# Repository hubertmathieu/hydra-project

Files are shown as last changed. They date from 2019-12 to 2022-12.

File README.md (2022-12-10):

# Hydra-Project

Répositoire du projet de serre hydroponique connectée du Cégep de Sorel-Tracy. 

## Introduction

Le projet repose sur une serre flottante qui puise l’eau nécessaire à même la rivière sur
laquelle elle repose. L’eau est filtrée et fertilisée par des engrais naturels solubles dans l’eau.
Elle est ensuite acheminée aux racines des plantes par un évaporateur. C’est une version
plus évoluée de l’hydroponie appelée aéroponie. Les plantes se nourrissent des nutriments
et relâchent dans la rivière une eau purifiée après condensation.

### Prérequis 

Vous trouverez ci-dessous la liste des matériaux ainsi que la liste des différents logiciels qui permettront de faire fonctionner le système d'automatisation de la serre. 
  
| Électronique | Tuyaux et plomberie | Serre et autres | 
| ---| --- | ---|
| [2x Relais 5V](https://amzn.to/2rm3FQe)| [Pompe à eau grand débit](https://amzn.to/2pLP6oq) | [Serre](https://amzn.to/33eJiS8) | 
| [6x Capteur d'humidité](https://amzn.to/2OKojkT) | [Pompe à eau petit débit](https://amzn.to/37F01RS) | [Scellant](https://bit.ly/37GrR0q) |
| [3x Capteur de pH](https://amzn.to/33jcuY7) | [Répartiteur de tuyaux](https://amzn.to/35Dt0nz) | [Disque rotatif](https://amzn.to/34mzRkX)| 
| [5x Capteur de niveau d'eau](https://amzn.to/2XVFi8h) | [3x Buse 50 microns](https://bit.ly/2DeN8js) | [Bac de rangement](https://bit.ly/34lHJTV) | 
| [1x FIPY](https://bit.ly/2KRR1iP) | [Ponceau 12po diamètre x 8po long](https://bit.ly/2OKOisl) | [pH Down](https://amzn.to/33lkYy6) | 
| [1x Filtreur](https://amzn.to/2XLTqAy) | [Rouleau de tuyeau en vinyle](https://bit.ly/33ljoMG) | [Engrais](https://amzn.to/2qJ6oTC) | 
| [2x Module Bluetooth](https://amzn.to/34l5aN6)| [Ruban d'étanchéité](https://amzn.to/2qKvdia) | |
| [9x Valves solénoïdes](https://amzn.to/2DeVWWT) | [50x Colliers de serrage en plastique](https://bit.ly/2KPPf1u) |
| [Convertisseur 12V-5V](https://amzn.to/2KV8RkR) | [Tuyeaux de cuivre (30' x 1/2")](https://bit.ly/2Djcwoq) | |
| [Convertisseur 12V-3.3V](https://amzn.to/2QRFST0) | | | 
| [Convertisseur 120V-12V](https://amzn.to/2QPPcqd) | | |
| [2x Arduino Uno Rev2](https://bit.ly/2pRjQEL) | | |
| [Panneau de distribution](https://amzn.to/2QPEYGv) | | | 
    
### Installation

La prochaine étape consiste à mettre sur pied un serveur Node Express. Nous avons utilisé la distribution Debian dans cet exemple. 

Installez nodeJS, Git et MongoDB, puis vérifiez la version de l'installation. 
```
$sudo apt-get update
$sudo apt-get install nodejs
$node -v
$sudo apt-get install git-all
```

Clonez le répositoire du projet. 
```
$git clone https://github.com/LudoB99/hydra-project.git
$cd hydra-project/backend
$npm install
$cd vendor
$npm install
```

Démarrez le serveur 
```
$cd hydra-project/backend
$docker compose up
```

## Écrit avec l'aide de:

* [NodeJS](https://nodejs.org/en/docs/) - Runtime JavaScript 
* [Express](https://expressjs.com/fr/) - Infrastructure Web
* [MongoDB](https://www.mongodb.com/fr) - Base de données

## Auteurs

* **[Cégep de Sorel-Tracy](https://cegepst.qc.ca)**
* Voyez aussi la liste des [contributeurs](https://github.com/LudoB99/hydra-project/graphs/contributors) qui ont participé au projet.

## License

This project is licensed under the MIT License - see the [LICENSE.md](LICENSE.md) file for details

## Remerciements

* À Alexandre Vovan pour ses conseils judicieux.
* Au [Camping-Marina Parc Bellerive](https://www.campingmarinabellerive.com/) pour leur hospitalité. 
* À la [SADC Pierre-de Saurel](https://sadcpierredesaurel.ca/) pour leur infinie générosité.

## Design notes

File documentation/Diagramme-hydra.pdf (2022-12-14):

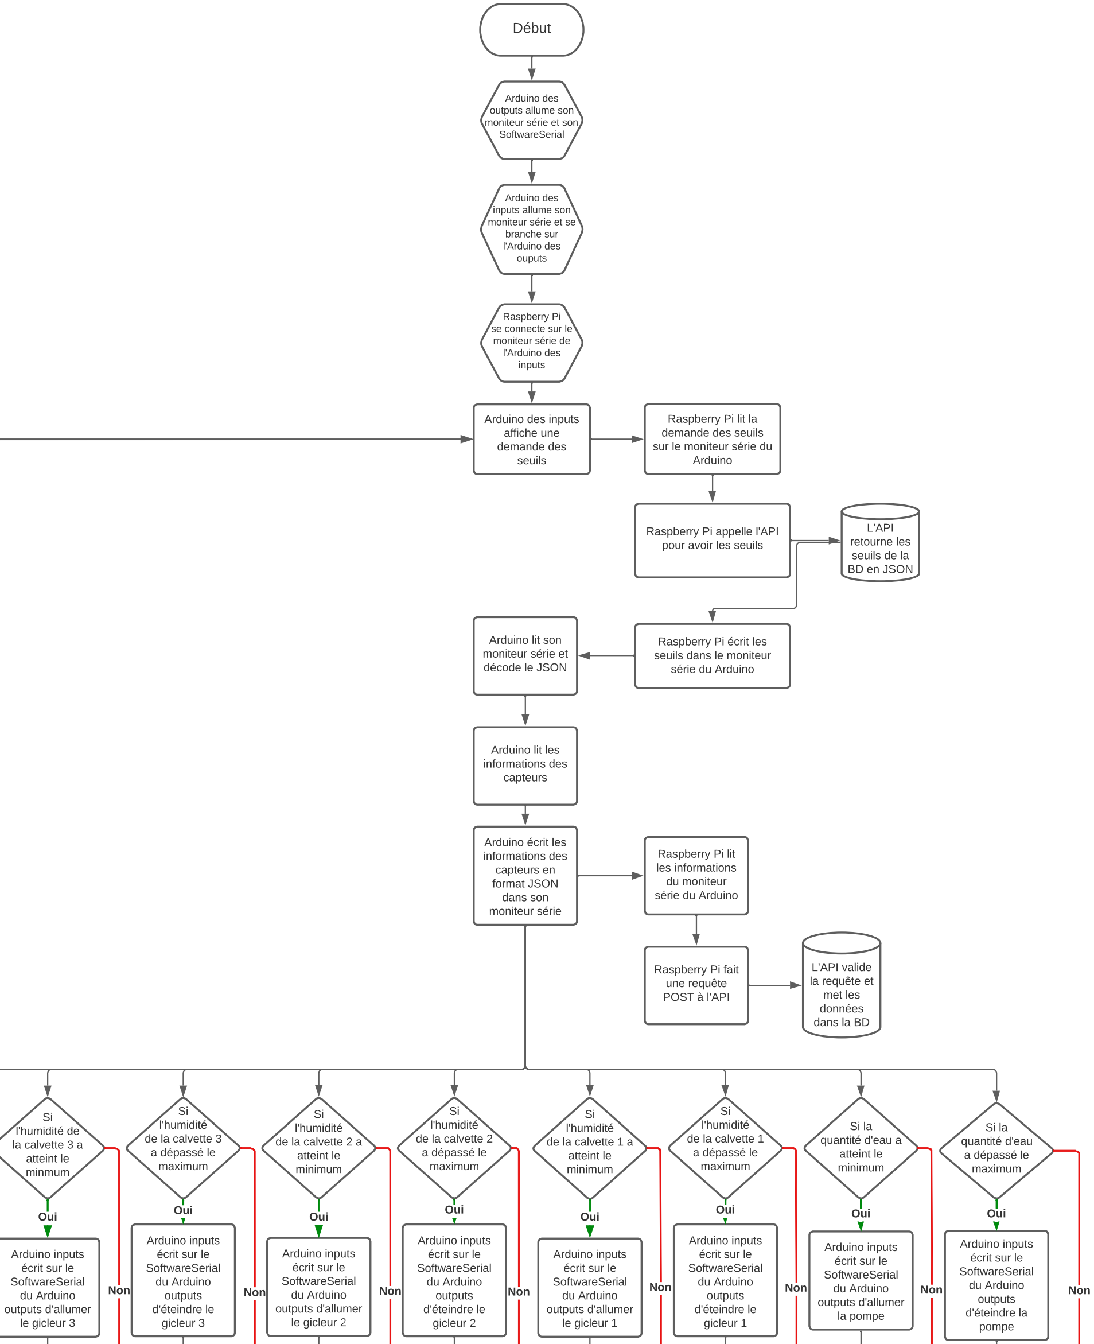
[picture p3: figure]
Début; Raspberry Pi se connecte sur le moniteur série de; l'Arduino des inputs; Arduino des inputs allume son moniteur série et se; branche sur l'Arduino des ouputs; Arduino des; SoftwareSerial; Arduino des inputs affiche une demande des seuils; Raspberry Pi lit la demande des seuils sur le moniteur série du Arduino; Raspberry Pi appelle l'API pour avoir les seuils; L'API retourne les seuils de la BD en JSON; Raspberry Pi écrit les seuils dans le moniteur série du Arduino; Arduino lit son moniteur série et; décode le JSON; Arduino lit les informations des capteurs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

outputs allume son moniteur série et son

Attente des
autres
décisions

Arduino des
outputs lit le
SoftwareSerial

Si le ph a
dépassé le maximum

Arduino inputs
écrit sur le
SoftwareSerial
du Arduino
outputs d'ajouter
du phDown

Oui
Arduino inputs
écrit sur le
SoftwareSerial
du Arduino
outputs de ne
pas ajouter du
phDown

Non

Si il
reçoit un message qu'il faut

éteindre la
pompe

Arduino des
outputs éteint la
pompe

Oui

Si il
reçoit un message qu'il

faut allumer la
pompe

Arduino des
outputs allume la
pompe

Oui

Attente des
autres
décisions

Si il
reçoit un message qu'il faut

éteindre le
gicleur 1

Arduino des
ouputs éteint le
gicleur 1

Oui

Si il
reçoit un message qu'il faut

allumer le
gicleur 1

Arduino des
outputs allume le
gicleur 1

Oui

Si il
reçoit un message qu'il faut

éteindre le
gicleur 2

Arduino des
outputs éteint le
gicleur 2

Oui

Si il
reçoit un message qu'il faut

allumer le
gicleur 2

Arduino des
outputs allume le
gicleur 2

Oui

Si il
reçoit un message qu'il faut

éteindre le
gicleur 3

Arduino des
outputs éteint le
gicleur 3

Oui

Si il
reçoit un message qu'il faut

allumer le
gicleur 3

Arduino des
outputs allume le
gicleur 3

Oui

Si il
reçoit un message qu'il faut

ajouter du
phDown

Arduino des
outputs ouvre la
valve du
phDown

Oui

Non | Non | Non | Non | Non | Non | Non | Non

Si il reçoit un message qu'il faut ne

pas ajouter du
phDown

Arduino des
outputs ferme la
valve du
phDown

Oui

Non | Non

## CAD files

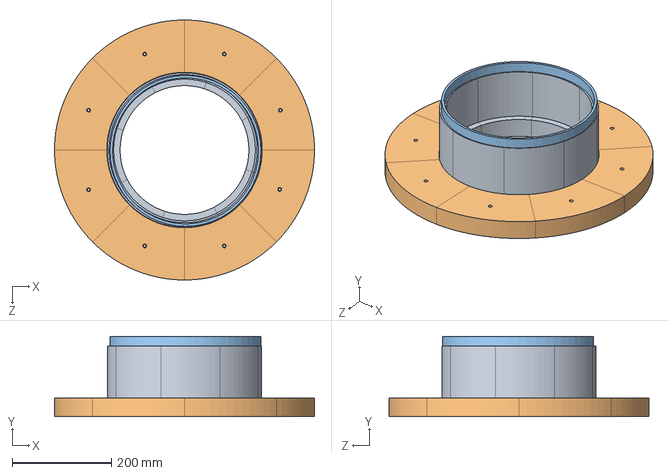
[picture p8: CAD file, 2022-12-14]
3D/Assemblage1.SLDASM
525.0 x 162.5 x 525.0 mm
base
interne

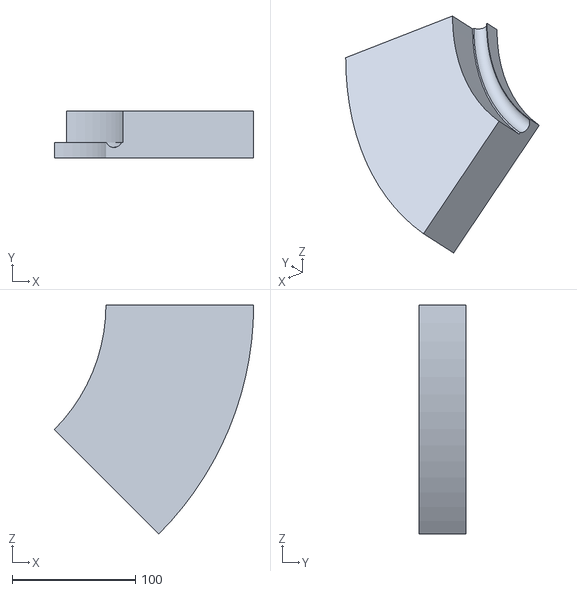
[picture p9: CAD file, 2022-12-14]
3D/base_section2.STL
161.6 x 38.1 x 185.6

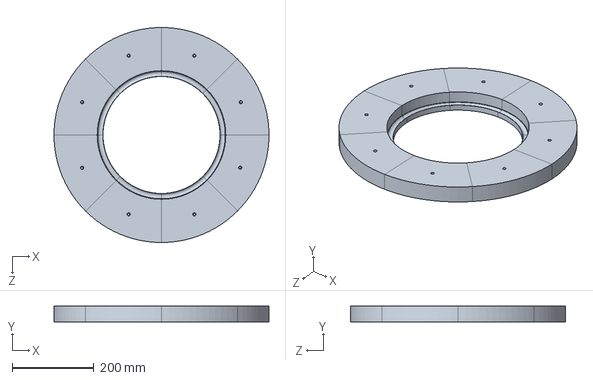
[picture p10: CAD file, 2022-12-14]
3D/base.SLDPRT
525.0 x 38.1 x 525.0 mm

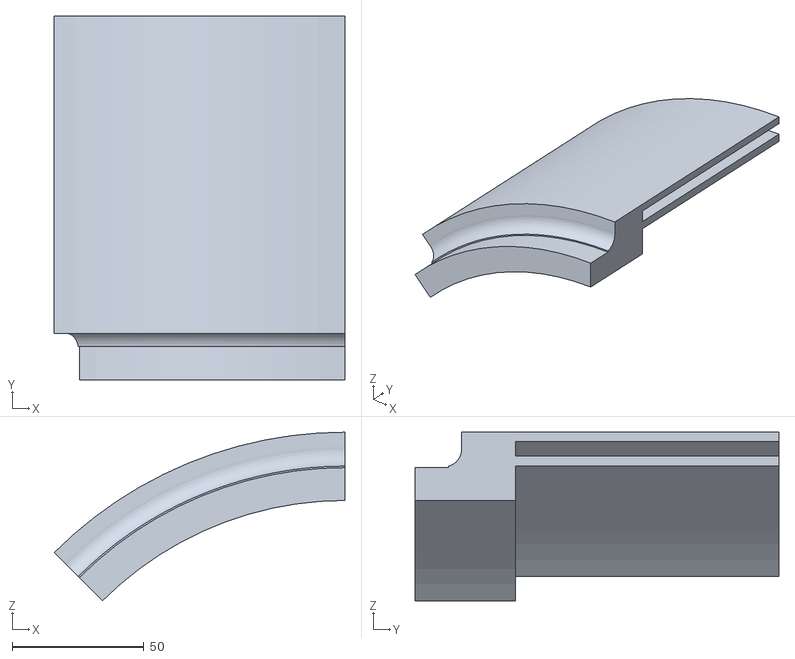
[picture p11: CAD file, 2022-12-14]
3D/interne_section5.STL
110.2 x 138.1 x 64.0

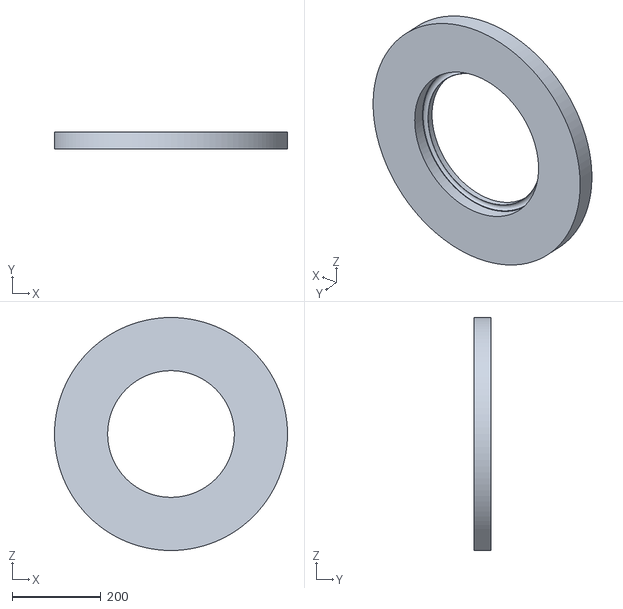
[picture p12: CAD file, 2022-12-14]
3D/base_section1.STL
525.0 x 38.1 x 525.0

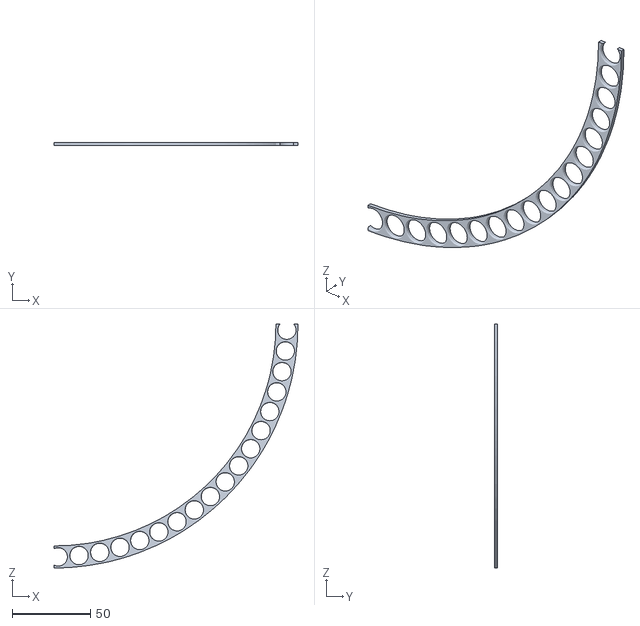
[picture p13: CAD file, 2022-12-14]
3D/Section 2 sup bille.STL
156.2 x 2.00 x 156.2

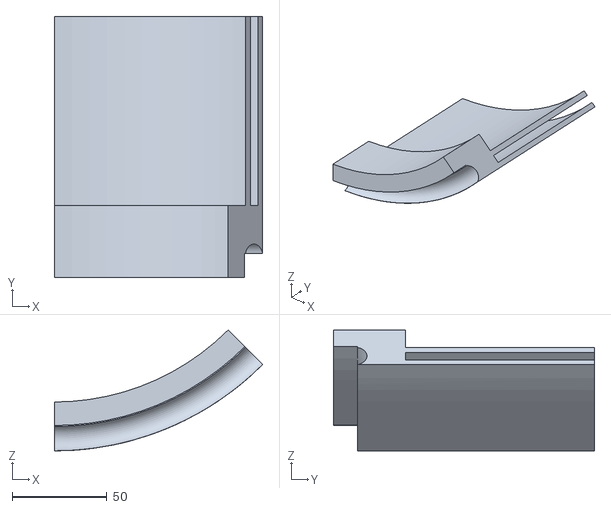
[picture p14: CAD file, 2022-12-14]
3D/interne_section1.STL
110.2 x 138.1 x 64.0

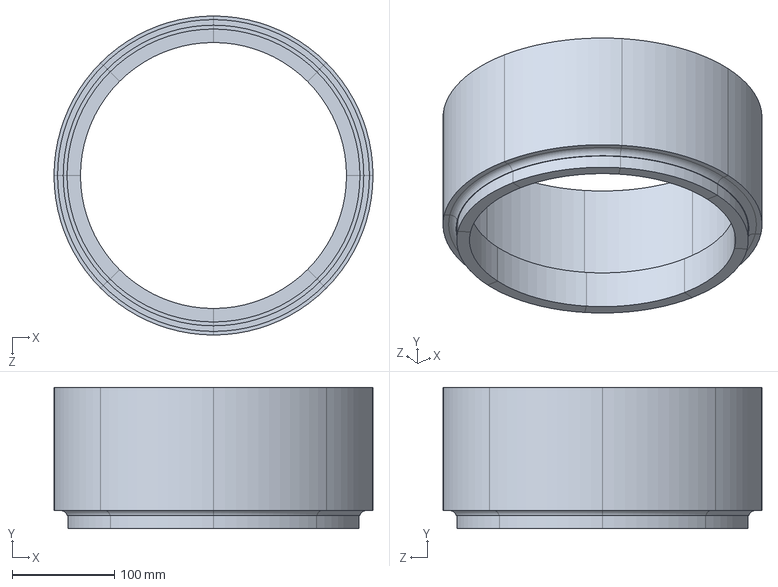
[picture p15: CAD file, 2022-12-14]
3D/interne.SLDPRT
311.8 x 138.1 x 311.8 mm

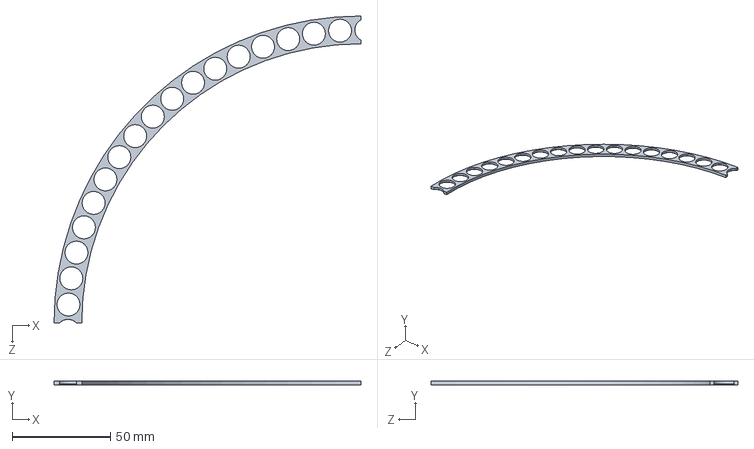
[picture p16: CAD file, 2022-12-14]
3D/support_bille.SLDPRT
156.2 x 2.00 x 156.2 mm

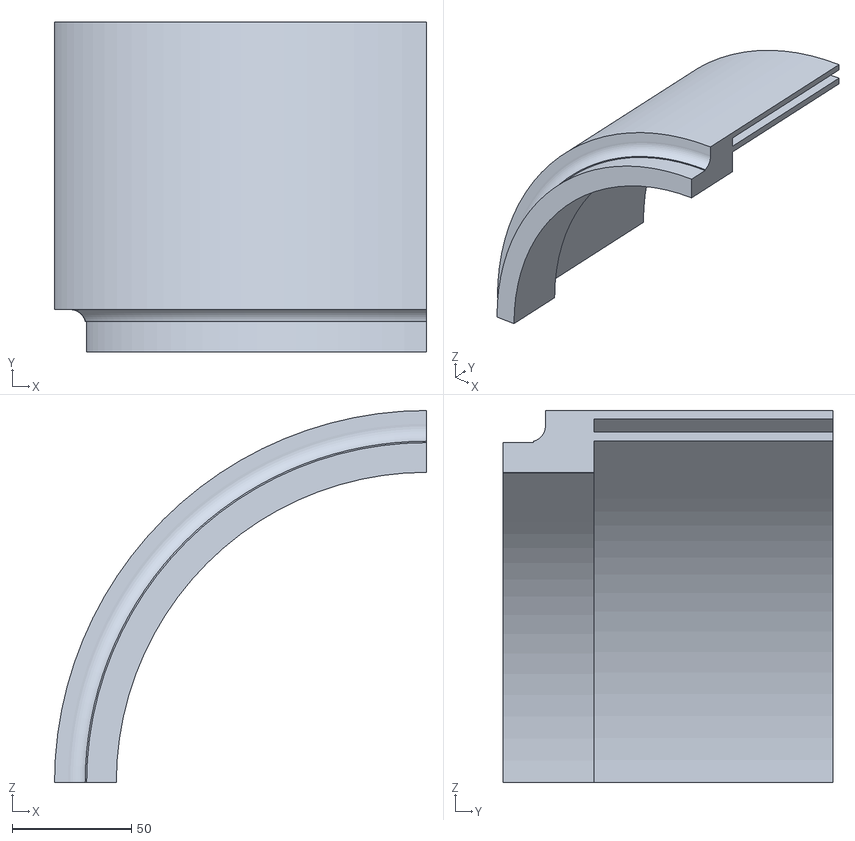
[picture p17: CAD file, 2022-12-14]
3D/base_section5.STL
155.9 x 138.1 x 155.9

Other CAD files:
3D/interne_section7.STL
3D/base_section8.STL
3D/interne_section8.STL
3D/interne_section4.STL
3D/base_section4.STL
3D/Section5_coupe.STL
3D/interne_section6.STL
3D/base_section7.STL
3D/Section 3 sup bille.STL
3D/Section 4 sup bille.STL
3D/UMS3_Section 2 sup bille.3mf
3D/base_section3.STL
3D/base_section6.STL
3D/interneV2.SLDPRT
3D/interne_section2.STL
3D/interne_section3.STL
3D/support_bille.STL
3D/tuyau.SLDPRT

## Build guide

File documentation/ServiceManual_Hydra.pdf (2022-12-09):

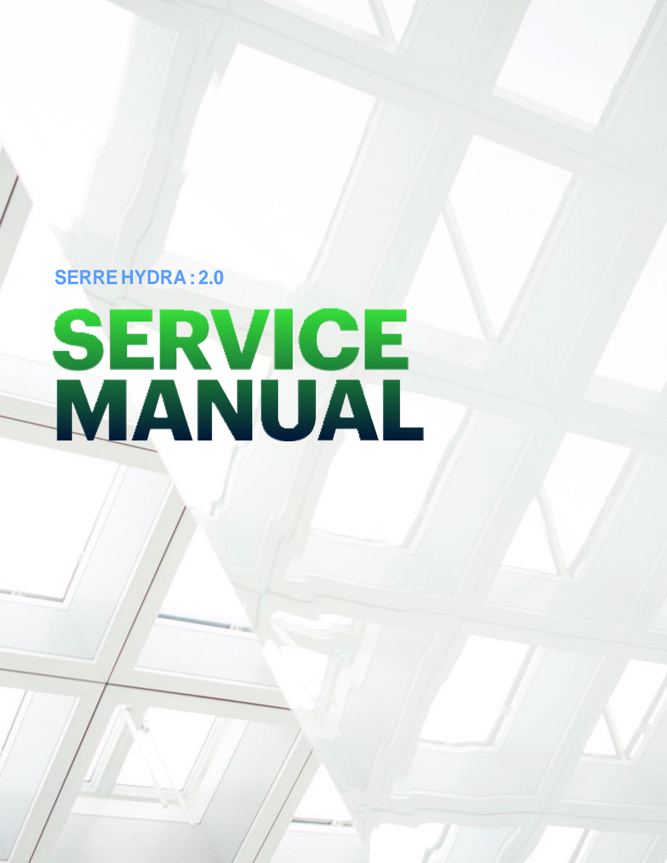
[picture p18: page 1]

## SERRE HYDRA : 2.0

## Table des matières

Table des matières | 2
Partie 1 : Physique | 6
Entretien de la serre | 6
Serre physique | 6
Serre palram | 6
Panneau | 6
Fenêtre | 6
Solidification | 7
Roulement à bille | 7
Entretien des composants | 7
Entrée d’eau | 7
Réservoir (eau filtrée et engrais) | 7
Filtreur | 8
Manuel d’utilisation | 8
Installation | 8
Tuyauterie | 9
Introduction | 9
Connecter la pompe 1 au système de filtreur | 10
Connecter la pompe 2 au système d’arrosage | 10
Pompes | 10
Introduction | 10
Emplacement | 10
Utilisation | 11
Système de burette | 11
Burette | 11
Aiguille | 11
Servomoteur | 12

Support à burette | | 13
Calvettes | | 13
Rotation des calvettes | | 13
Calvettes physiques | | 13
Partie 2 : Électronique | | 14
La boîte de relais | | 14
Entretien des capteurs | 14 DHT11 | 14
Capteur de niveau d’eau | 15
Capteur de ph | 16
Relais | 16

Servo
-moteurs | 17
Partie 3 : informatique | 18
Maintenance de l’app mobile | 18
Survol de l’application | 18
Recevoir les données du serveur | 19
Envoyer les données au serveur | 20
Données sur la température ambiante | 21
L’intervalle entre les requêtes | 21
Conversion JSON en object | 22
Page des views | 23
Interface utilisateur | 24
Maintenance du serveur | 25
Base de données | 25
Méthodes utilisées | 26
GET | 26
POST | 26
Maintenance des microcontrôleurs | 27
Relier les arduinos | 27

Reprogrammer un Arduino | 27
Connexions sérielles | 28
Les pins | 29
Les seuils | 30
Les lectures | 31
Les commandes | 32
L’ajout d’engrais | 32
Le temps de déversement des engrais | 33
L’envoie de données au Raspberry Pi | 34
La réception des données | 35
Communication externe (Raspberry Pi) | 36
Le physique | 36
La connexion au Arduino | 36
La connexion Wifi | 36
L’alimentation | 36
Perte de connexion (dépannage) | 36
Schéma de communications | 37
Explication générale | 37
#1 Arduino | 37

#2 Raspberry Pi | 38

#4 Serveur | 38

#5Application mobile | 38

6

## Partie 1 : Physique

## Entretien de la serre

Serre physique
Serre palram
Pour toute question sur l’installation, l’entretien et la maintenance de la serre, veuillez-vous référer au manuel d’utilisation de ce dernier : https://www.shedsforlessdirect.com/manuals/Palram-6x8-Mythos-Hobby-Greenhouse-hg5008g-Manual.pdf. (https://www.shedsforlessdirect.com/manuals/Palram-6x8-Mythos-Hobby-Greenhouse-hg5008g-Manual.pdf)

Panneau
Dans l’éventualité qu’un panneau de poly carbonate soit emportée par le vent lors d’une dure tempête. Il est possible de le remplacer en acheter des panneaux de poly carbonate transparent et de le couper selon les mesures du panneau perdu.

Fenêtre
Il est également possible le mécanisme de la

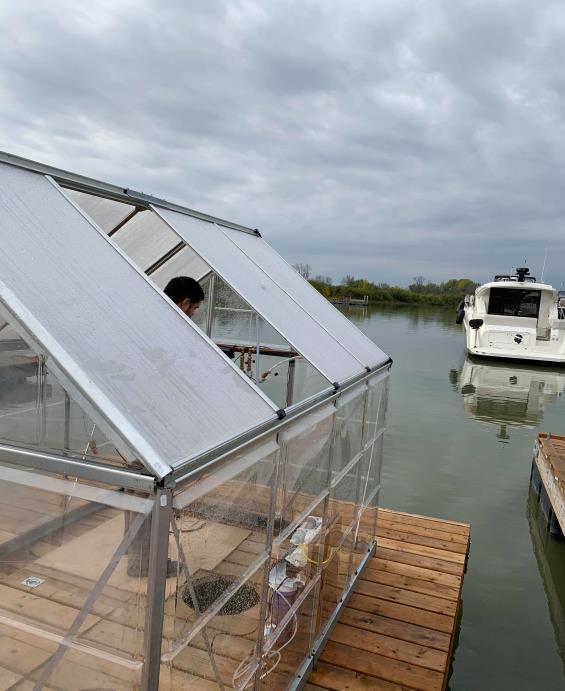
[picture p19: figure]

fenêtre original se brise. Dans un | Exemple d’un panneau envolé
tel cas, il est possible de le réparer relativement simplement en fixant le mécanisme avec des vis.

7

Solidification
Puisque la serre est située sur un quai sur la rivière Richelieu, il est possible qu’elle fasse face à de vent violent qui pourraient endommager drastiquement la serre. Pour remédier à ce problème, il devrait avoir une solidification de la serre. Chaque tuile du toit devrait avoir des trous pour y faire passer des « tie-wrap ». Ces « tie-wrap » devraient attacher chaque tuile voisine question de les connecter et de les empêcher de partir au vent. De plus, la structure de la serre devrait être renforcée avec des poteaux de métal supplémentaires positionnés diagonalement.

Roulement à bille

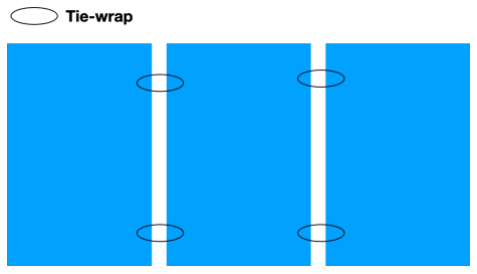
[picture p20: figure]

Dans le cas où un des roulements à bille brise, vous pouvez remplacer seulement la pièce manquante. Le fichier avec chacune des composantes se trouve dans le GitHub du projet. Les billes utilisées dans le roulement sont des billes en acier inoxydable d’un demi pouce (voir dans la liste de pièces sur le GitHub).

## Entretien des composants

Entrée d’eau
Dans le cas d’un problème lié à l’entrée de l’eau sous la serre, veuillez vérifier sous la clavette la plus près du bac d’eau. Vous retrouverez une plaque en aluminium arborant une pompe. Cette dernière peut être remplacer

Réservoir (eau filtrée et engrais)
Si un bris survient avec le réservoir, vous devez acheter un bac avec une capacité de 53L et y percer un trou inférieur à 3/8’’ au milieu du bac. Par la suite vous devez coller en dessous du bac un adaptateur mâle femelle vis-à-vis avec le trou à l’aide de la colle goop marine et attendre 24h avant d’y retoucher. Ensuite, vous pouvez réparer les pattes de bois au bac en pré perçant le bac et les pattes et après visser les pattes de bois au bac avec délicatesse. Important : appliquer de la goop sur chaque trou, mettre un « washer », rappliquer de la goop pour ensuite visser. Il restera à visser les pattes du bac en les accotant sur le support à burettes.

8

Filtreur
Manuel d’utilisation

Pour tout questionnement technique à propos du filtre, allez visiter le manuel d’instruction suivant :
https://www.123filter.com/ac/kb/ISPRING%20Residential%20RO%20manual%20Version %202015-6.pdf. (CONSEIL : lire le manuel avant l’installation)

Installation
Accrocher le filtreur sur le support de bois en photo ci-dessous grâce aux trous dans la base de métal et les vis qui sont fixées sur la structure de bois. Pour l’installation, il ne faut pas le connecter à la bonbonne d’eau puisque l’eau ira directement dans le bac. Assurer vous les deux fils du filtreur sont branchés avant de l’utiliser. IMPORTANT : vider l’eau des réservoirs du filtreur lors de gel, s’assurer que les tuyaux sont toujours bien connectés à leur embout. Le tuyau de sortie doit se vider dans le réservoir principal de la serre.

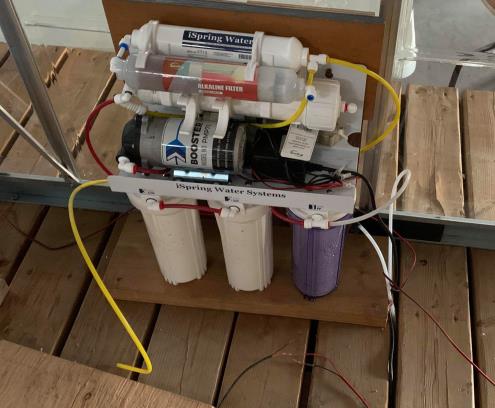
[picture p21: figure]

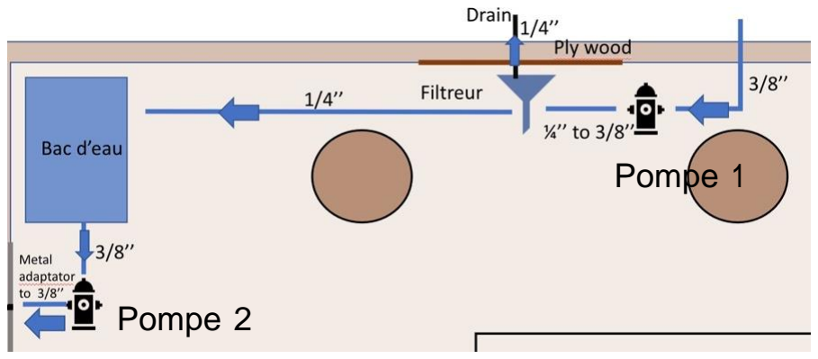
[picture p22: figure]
Pompe 1; Pompe 2

9

Tuyauterie

Introduction
S’assurer qu’à chaque fois que vous connectez un tuyau avec un
autre pièce pour y faire passer un liquide, vous y ajoutez un « hose-clamp » pour s’assurer de l’étanchéité des connexions. Visser la bien fort et accoter la bien à l'extrémité du tuyau.

Mettre au bout de l’embout qui sera connecté au tuyau du Téflon,
appliquez une à deux couches sur toute la surface dans le sens horaire
(visser). Ceci assurera aussi une étanchéité des connexions.

Si vous devez connecter deux tuyaux de différentes tailles, utiliser les

adaptateurs femelle-femelle en métal correspondant aux tailles des tuyaux (ex : 3/8 à 1/2).

Si vous désirez connecter un tuyau à un tuyau de métal ayant des filets, veuillez utiliser des adaptateurs femelles et males avec les bonnes tailles.

Si vous désirez connecter deux tuyaux de métal ayant des filets, veuillez utiliser des adaptateurs mâles vers mâles de bonne taille.

Pour fixer les tuyaux à la serre, vous devez utiliser des serre-joints. Vous devez
en mettre au minimum à chaque mètre de tuyaux. Vous devez les serrer en clouant ou en vissant de chaque côté des serre-joints.

10

Connecter la pompe 1 au système de filtreur
Il vous faut une longueur voulue de tuyau de taille 3/8’’ pour les connecter aux deux embouts de la pompe. Ajouter de téflon aux deux embouts et lorsque les tuyaux sont fixés, serrer la connexion avec des « hose-clamp ». Le tuyau entrant du filtrer doit être de taille 1/4’’ et doit être connecté au tuyau de la pompe sortant grâce aux adaptateurs.

Connecter la pompe 2 au système d’arrosage
Il vous aussi la quantité désirée de tuyaux 3/8’’ à connecter à la pompe par les deux embouts de la pompe. Après avoir connecté les tuyaux à la pompe, vous devez insérer le tuyau (entrant) de la pompe à la connexion de métal situé en dessous du bac bleu (réservoir). Le tuyau (sortant) de la pompe doit être connecté au tuyau de métal (entrant) d’arrosage grâce aux adaptateurs.

Pompes
Introduction
Le système comprend 2 pompes, la pompe #1 : 5L/min, la pompe #2 : 24L/min. Ces deux pompes doivent être remplies d’eau avant de les démarrer. Aussi, avant l’hiver, il faut vider l’eau restante dans les pompes.

Emplacement
La pompe #1 doit être fixée en dessous à gauche du réservoir en ayant les tuyaux vers l’extérieur du bac. La pompe #2 doit être fixée sur une barre de métal vissée en dessous du quai. La plaque de métal est d’environ 10/70cm et est vissée sur sa longueur sur les parois intérieures du quai en dessous d’un des trous de calvettes. Pour visser les pompes, il y a sur eux des petites « pattes » avec des trous pour y insérer des vis et visser ceux-ci.

11

Utilisation
La pompe #1 sert à transporter l’eau qui contient les engrais du réservoir jusqu’au système des buses. Puisqu’il n’est pas nécessaire d’avoir une grosse pression pour y amener cette eau il est conseillé d’utiliser cette pompe de 5L/min. La pompe #2 doit transporter l’eau de la rivière jusqu’au filtreur. Pour faire cette opération, il est recommandé d’utiliser une pompe au-dessus de 20L/min puisque qu’une grande résistance est appliquée par l’entrée d’eau du filtreur. IMPORTANT : le filtreur n’est pas compris avec, la pompe #2 est essentielle à l’entièreté du système.

Système de burette
Burette
En cas de bris de burette, il est possible d’effectuer un remplacement en commander une burette 50ml puis en la sectionnant à la ligne de 35 ml. Important de noter qu’il est préférable de sectionner ces dernières avec des outils spécialisés pour éviter un bris imprévu.

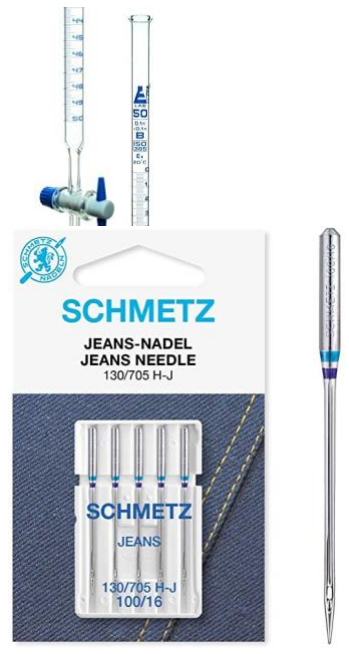
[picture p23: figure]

Aiguille
En cas de perte d’une aiguille, vérifier dans la boîte étanche qu’il n’en reste effectivement plus avant d’en commander. Il est important d’ajouter de l’adhésif à usage maritime (Goop) aux 2 extrémités de ces dernières pour s’assurer de leur maintien (voir figure #1).

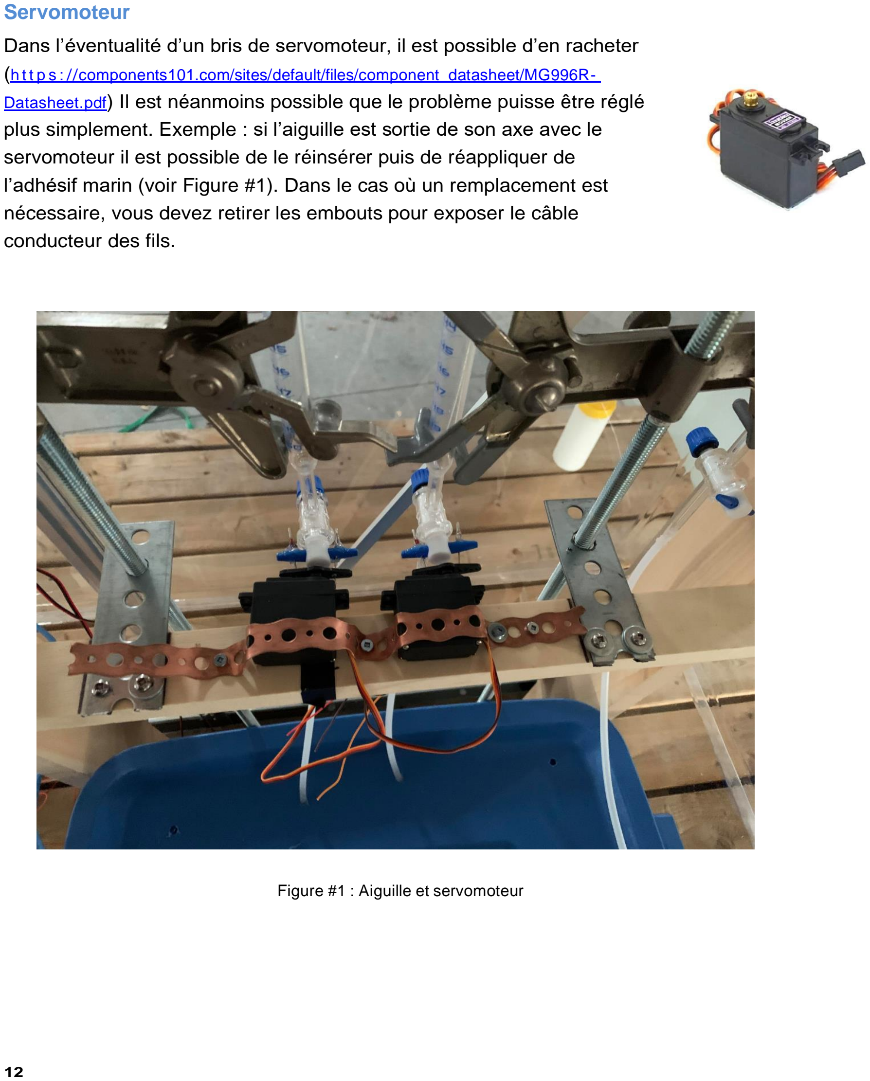
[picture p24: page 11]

12

Servomoteur

Dans l’éventualité d’un bris de servomoteur, il est possible d’en racheter

(h t t p s : //components101.com/sites/default/files/component_datasheet/MG996R-
Datasheet.pdf) (https://components101.com/sites/default/files/component_datasheet/MG996R-%20Datasheet.pdf) Il est néanmoins possible que le problème puisse être réglé plus simplement. Exemple : si l’aiguille est sortie de son axe avec le servomoteur il est possible de le réinsérer puis de réappliquer de l’adhésif marin (voir Figure #1). Dans le cas où un remplacement est nécessaire, vous devez retirer les embouts pour exposer le câble conducteur des fils.

Figure #1 : Aiguille et servomoteur

13

Support à burette
Les supports à burettes sont composés de 2 parties, premièrement une tige métallique filetée de diamètre 7/16’’ et de pince à burette de laboratoire. Les premières sont trouvables dans toutes bonnes quincailleries et ne nécessitent aucune manipulation supplémentaire pour les remplacer. Les seconds devront être commandés en ligne dans l’éventualité d’un bris. Il sera toutefois nécessaire de retirer la planche supportant les servomoteurs avant d’installer l’une ou l’autre des pièces.

Calvettes

Rotation des calvettes
Il est possible que le roulement à billes qui permettent la rotation des calvettes soient bloquées par des débris ou par l’oxydation. Pour résoudre ce problème, 2 options émergent : remplacer la pièce défectueuse ou les graisser. Dans le premier cas, le roulement peut être usiné à partir du document qui se trouve si le GitHub du projet. Dans l’autre cas, de la graisse standard peut être appliquée pour permettre une rotation.

Calvettes physiques

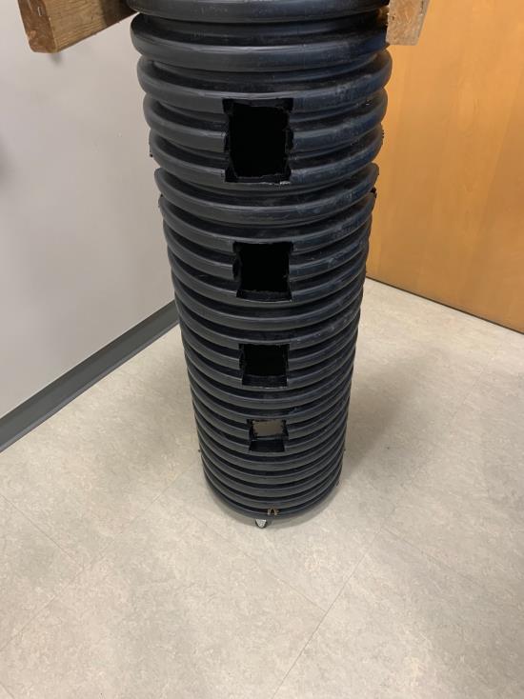
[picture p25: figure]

Si dans un cas extrême une clavette doit être remplacée, ces dernières sont en réalité des ponceaux de 16’’. Il sera nécessaire par la suite de trouer ce dernier pour pouvoir y insérer les pots à plantes.

14

## Partie 2 : Électronique

## La boîte de relais

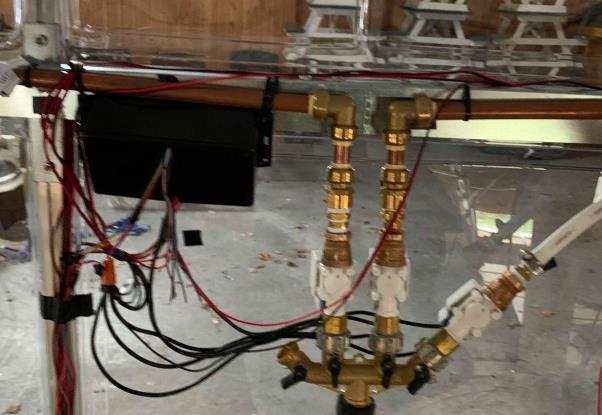
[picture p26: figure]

La boîte de relais se situe près des valves et s’occupe d’activer la pompe du filtreur, la pompe des buses ainsi que les 3 valves qui contrôle les buses. Les câbles noirs sont le responsable pour la mise à terre « ground ». Les câbles en dessous de la boite qui contient les relais alimente les relais avec du 12V. Les câbles sortant du haut de la boîte de relais sont utilisés afin de contrôler les relais. Chaque couleur a un contrôle sur un élément différent de la serre.

Rouge : Pompe du filtreur
Jaune : Pompe des buses
Orange : La buse numéro 1 (valve de gauche)
Vert : | La buse numéro 2 (valve au centre)
Bleu : | La buse numéro 3 (valve de droite)

## Entretien des capteurs

DHT11
Cette pièce sert à mesurer la température en degrés Celsius et le pourcentage d’humidité. La tige avec le symbole « + » doit être reliée à l’entrée 5 volts du Arduino, la tige avec le symbole « - » doit être reliée au « ground » du Arduino et la tige avec le symbole « OUT » doit être

reliée à la tige identifiée DHT11_PIN, SECOND_DHT11_PIN ou THIRD_DHT11_PIN
dans le code du microcontrôleur appelé Input Arduino.

15

La pièce est collée avec du goop sur chacune des buses et les fils doivent passer par le tuyau de la buse pour éviter de les déchirer lors des rotations de la calvette.

Capteur de niveau d’eau

Cette pièce doit être fixée à la verticale, les trois pins vers le haut, et permet de lire un entier entre 0 et 625 correspondants à la portion de la pièce qui est trempée dans l’eau.

La pin - doit être reliée au ground du Arduino des input et le pin

S, au pin noté WATER_SENSOR_PIN ou WATER_SENSOR2_PIN dans le code du InputArduino. Il est important de noter que, pour éviter des problèmes de corrosion, la tige « + » de la pièce n’est pas reliée au 5 volts du Arduino, mais bien à la pin notée WATER_SENSOR_POWER_PIN ou WATER_SENSOR2_POWER_PIN. Ainsi, le capteur n’est pas continuellement alimenté, mais est alimenté seulement lors
de la prise de lectures.

Deux de ces pièces sont fixées dans le bac d’eau avec de la goop. Il est important que le capteur correspondant à waterLevel1 dans le code ait celui du haut, et que le capteur correspondant à waterLevel2 dans le code soit celui du bas.

Le capteur du haut ne doit pas être fixé en haut complètement, pour laisser du jeu pour l’ajout d’engrais et
pour le temps de réaction du filtreur et de l’entrée d’eau.

Il faut toujours s’assurer que les connexions entre les fils et le capteur soient scellées avec du goop pour les protéger de l’eau.

16

Capteur de ph
Ce capteur prend des mesures de pH dans le bac d’eau et la valeur lue dans la variable phValue du Arduino des input correspond à la moyenne des mesures prises par le capteur à chaque itération du Arduino. Le tube du capteur doit être relié
à la puce par la connexion correspondante.

La pin VCC doit être relié au 5v du Arduino des input. Il y a deux pins ground qui doivent être reliés au ground du Arduino, une pour le tube et une pour la puce. Finalement, la pin P0 doit être reliée à la pin notée PH_SENSOR dans le code du InputArduino. Les pins T0 et D0 ne seront pas utilisés.

La puce doit être fixée avec de la goop à l’extérieur du bac, et le tube doit être à l’intérieur du bac.

Relais
Cette pièce sert à activer et désactiver les pompes et les valves selon un courant analogue envoyé par le Arduino. Du côté des pins, on doit reliée celle notée « + » ou VCC au 5 volts du Arduino des outputs, la pin noté gnd au ground de ce Arduino, et l’autre à la pin identifié par FILTER_PUMP_RELAY_PIN (pour la pompe qui active l’entrée d’eau et le filtreur), SPRAYER_PUMP_RELAY_PIN (pour la pompe qui envoie l’eau aux buses) ou à une des trois pins identifiés par SPRAYER_SWITCH_PIN (les relais qui activent les
valves pour chacune des trois buses).

De l’autre côté du relais (celui sur la photo), il y a 3 entrées pour le fil sectionné alimentant le dispositif voulu. Il faut insérer les 2 sections de fils dans les deux entrées identifiées par un dessin de circuit fermé. Ainsi, lorsque le Arduino va envoyer du courant, le circuit va être ouvert (les dispositifs désactivés) et lorsque le Arduino va arrêter d’envoyer du courant, le circuit va être fermé et le dispositif correspondant, activé.

17

Servo-moteurs
Cette pièce sert à ouvrir et fermer les valves des burettes qui distribuent l’engrais. Il faut choisir une tête de servomoteur à 2 pales et relier ces pales à la valve de la burette à l’aide
d’aiguilles.

Le servomoteur a 3 fils. Celui noté + doit être relié au 5 volts du Arduino des outputs, celui noté « - » au ground du Arduino, et le 3e à la tige identifiée par SERVO1_PIN, SERVO2_PIN, SERVO3_PIN ou SERVO4_PIN dans le code du OutputArduino.

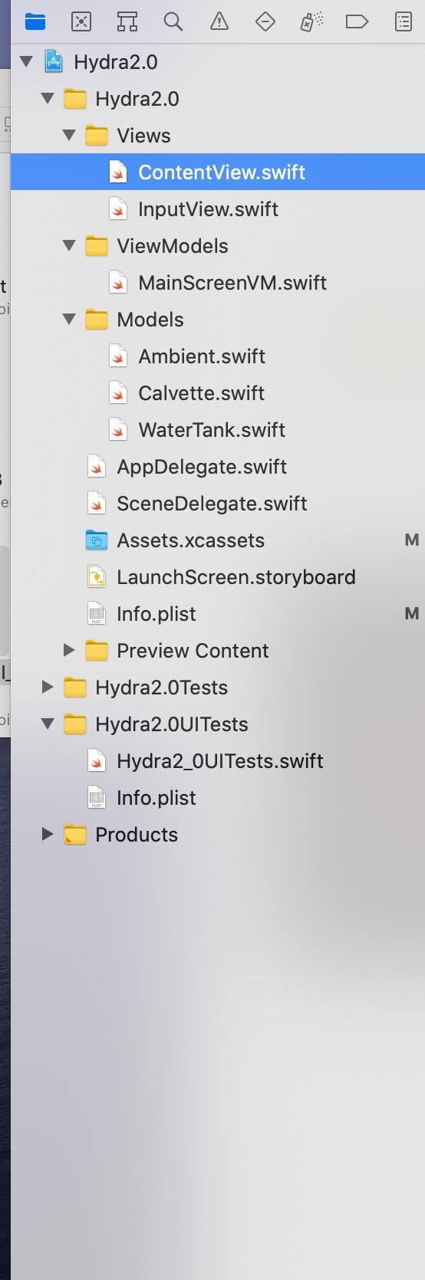
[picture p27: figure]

18

## Partie 3 : informatique

## Maintenance de l’app mobile

Survol de l’application

Cliquez sur l’icône de dossier (ici en bleu en haut à gauche) pour faire apparaître l’arborescence des fichiers de l’application.

Dans le dossier « Views » se trouvent les fichiers qui définissent l’aspect visuel de l’application.
« ContentView.swift » représente la page d’accueil et « InputView.swift », la page des configurations.

Dans le dossier « Models » se trouvent les classes qui contiennent les données de l’application à un moment précis, ainsi que les fonctions qui créent ces données à partir des réponses obtenues du serveur.

Dans le dossier « ViewModels » se trouve le fichier
« MainScreenVM.swift », qui effectue les requêtes au serveur.

Finalement, dans le dossier « Assets.xcassets » se trouvent les images associées à l’application.

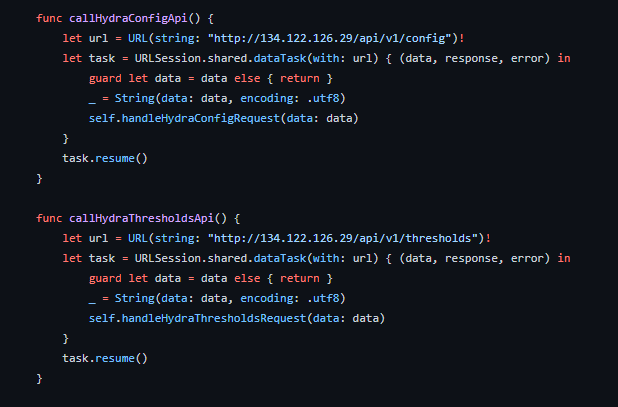
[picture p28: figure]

19

Recevoir les données du serveur

Voici les requêtes qui vont chercher les données sur la serre du serveur. Les deux URL correspondent à l’adresse du serveur.

20

Envoyer les données au serveur

Voici la requête qui est effectuée lorsque vous appuyez sur le bouton sauvegarder de l’écran des configurations.

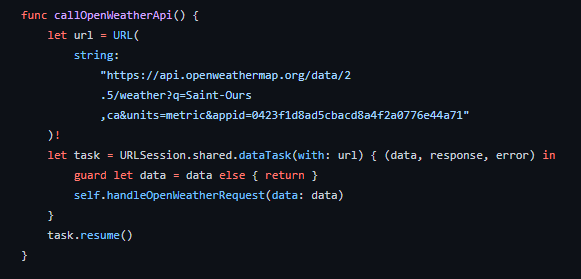
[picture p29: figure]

21

Données sur la température ambiante

L’application effectue des requêtes à « OpenWeatherMapAPI » pour connaître la température et l’humidité ambiantes. Si vous pensez déménager la serre, vous n’avez qu’à changer le nom de la localité dans l’URL de la requête.

L’intervalle entre les requêtes

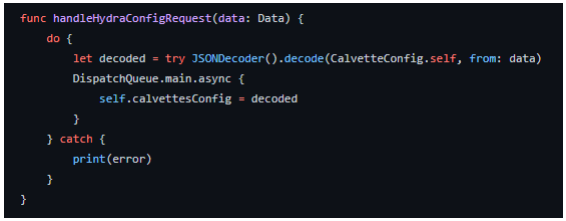
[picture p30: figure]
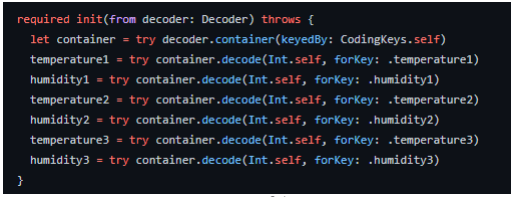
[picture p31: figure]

22

Ceci peut être très intéressant à connaître pour l’utilisateur. Ici, vous pouvez changer la valeur de la variable « timeInterval » qui correspond au temps en secondes entre chaque requête au serveur.

Conversion JSON en object

Fichier MainScreenVM

Fichier Calvette

Ce sont ces fonctions qui convertissent l’objet Json reçu du serveur en un objet constitué de classes qui est utilisable dans les fichiers Views.

23

Page des views

L’application a été construite à partir de « SwiftUI ». Si vous avez les connaissances nécessaires, c’est sur les pages « ContentView » et « InputView » que vous pourrez configurer le look de l’application.

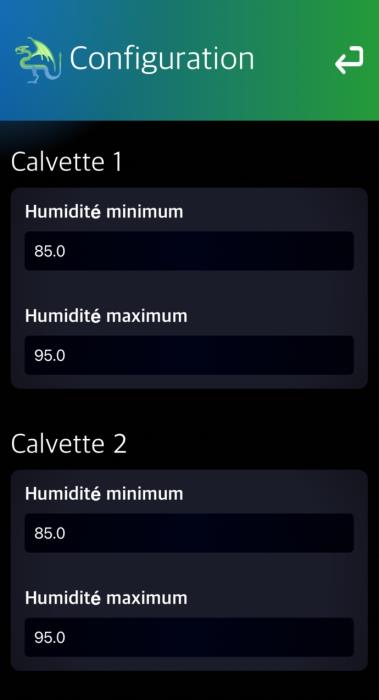
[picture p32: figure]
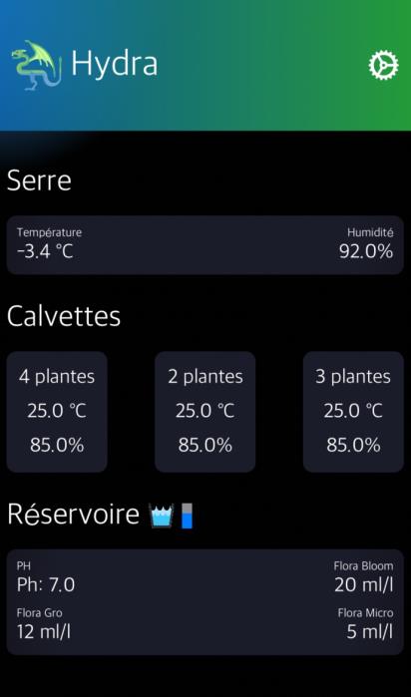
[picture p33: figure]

24

Interface utilisateur

Voici la manière qu’est affichée les informations que serveur reçoit de la serre. Sur cette page il y a la température, l’humidité de l’endroit (extérieur), les informations sur les calvettes (température et humidité). Sur la page de configuration on peut modifier les infos sur les calvettes.

25

## Maintenance du serveur

Base de données

La base de données étant basée sur « mongodb » n’est pas un schéma relationnel, mais bien « nosql ». Soit un objet JSON qui est modifié et réinséré dans la base de données. Il a deux collections, une pour les données de la serre (config) et une pour les thresholds de la serre.

Pour y accéder, le nom de la base de données et Hydra et la collection utilisée se nomment « threshold ». L’objet json config va s’en suit :

1- La température de la calvette # 1

2- La température de la calvette # 2

3- La température de la calvette # 2

4- L’humidité actuelle de l’humidité de la calvette #1

5- L’humidité actuelle de l’humidité de la calvette #2

6- L’humidité actuelle de l’humidité de la calvette #3

7- Le ph du bac d’eau

8- Le niveau de l’eau du capteur #1

9- Le niveau de l’eau du capteur #2

L’objet json threshold va s’en suit:

1- La valeur maximale de l’humidité de la calvette #1

2- La valeur minimale de l’humidité de la calvette #1

3- La valeur maximale de l’humidité de la calvette #2

4- La valeur minimale de l’humidité de la calvette #2

5- La valeur maximale de l’humidité de la calvette #3

6- La valeur minimale de l’humidité de la calvette #3

7- Le ph désiré du bac

26

Méthodes utilisées

Pour la plupart des utilisations nécessaires pour le fonctionnement de la serre, il ne suffit que de 2 requêtes HTTP pour afficher et modifier les données. Une se servant de la méthode GET et l’autre POST.

GET

Pour accéder aux informations actuelles de la serre vous pouvez effectuer une requête HTTP à cette URL : http://134.122.126.29/api/v1/config/ (http://134.122.126.29/api/v1/Threshold/) ou http://134.122.126.29/api/v1/thresholds/
Les données sont renvoyées selon l’objet énoncé plus haut.

POST

Pour effectuer des modifications sur la base de données veuillez effectuer une requête POST sur la même URL soit : http://134.122.126.29/api/config/ ou http://134.122.126.29/api/thresholds/
La réponse à cette requête si tout c’est bien passé est le revoie de l’objet.

27

## Maintenance des microcontrôleurs

Relier les arduinos

On utilise 2 Arduino. Le premier récolte les données et les envoie au Raspberry Pi, et envoie aussi des commandes à l’autre Arduino. Le deuxième reçoit les commandes de l’Arduino des inputs et s’en sert pour activer les relais et les servomoteurs.

Les deux « Arduinos » doivent être reliés ensemble selon la méthode décrite plus loin dans la section LES CONNEXIONS SÉRIELLES.

Reprogrammer un Arduino

Si vous voulez effectuer des manipulations dans le code, il faut tout d’abord savoir reprogrammer le Arduino pour que ces modifications s’appliquent. Pour ce faire, aller dans l’onglet Outils du menu. Choisissez :

Le type de carte : Arduino Uno

Le port : Arduino ISP pour le Uno

Le programmateur Arduino ISP pour le Uno

Ensuite, il suffit de choisir téléverser dans le menu Croquis pour effectuer la programmation.

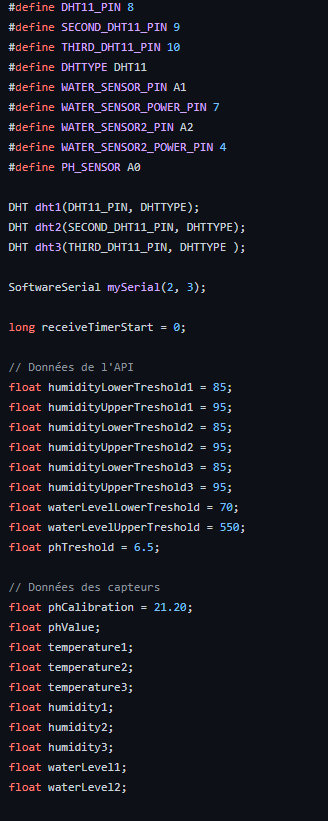
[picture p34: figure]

28

Connexions sérielles

Arduino des Input

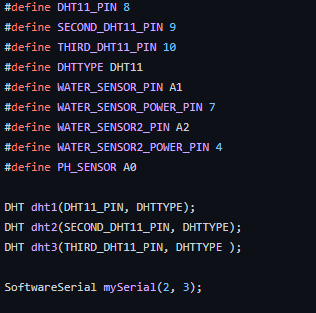
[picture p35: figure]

29

On utilise la librairie « SoftwareSerial » pour créer des ports sériels supplémentaires. Ainsi, le port de base (Serial), reste réservé pour l’envoi de données au Raspberry Pi.

Le port « mySerial » sert à la communication entre les 2 « Arduinos ». Dans le code ci-dessus, on voit que le RX (receveur) du Arduino des input correspond à la pin 2 et le TX (transmetteur) à la pin 3. Sur le Arduino des outputs, le RX de « mySerial » correspond à la pin 2, et le TX à la pin 3.

Il est important de relier le RX d’un Arduino au TX de l’autre Arduino et vice-versa. Ainsi, si on ne modifie pas le port sériel, la pin 2 de l’Arduino des inputs sera reliée à la pin 3 de l’Arduino des outputs, et la pin 3 de l’Arduino des inputs sera reliée à la pin 2 de l’Arduino des outputs.

Les pins

Ici, vous pouvez changer l’endroit où se connecte chaque capteur sur le Arduino. Voir la section sur les capteurs pour savoir quelle variable correspond à quel capteur.

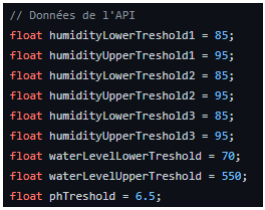
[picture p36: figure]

30

Les seuils

Vous pouvez changer ici les seuils correspondant à l’activation des relais et des servomoteurs. Le seuil d’humidité minimum active la buse d’arrosage. Le seuil d’humidité maximum la désactive. Le seuil de niveau d’eau minimum active la pompe du filtreur et celui du niveau d’eau maximum la désactive. Finalement, le seuil de pH active l’ajout de « pHDown ».

31

Les lectures

Arduino des inputs

Ce sont ces fonctions sur l’Arduino des inputs qui permet de prendre les mesures. Veuillez noter que pour le pH, il y a une fonction pour trier les lectures (bSort) et une fonction pour calculer la moyenne des lectures (calculateAveragePh). Ainsi, la valeur de pH obtenue à chaque itération du Arduino est une moyenne.

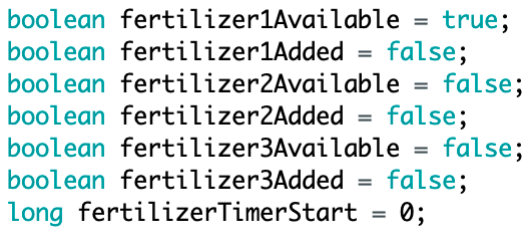
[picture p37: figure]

32

Les commandes

Arduino des inputs

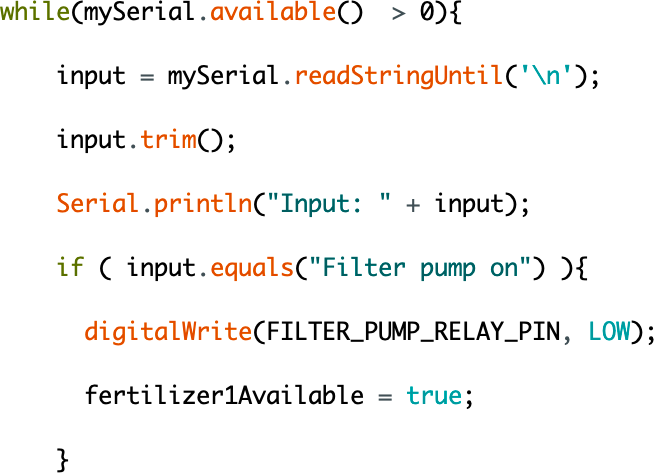
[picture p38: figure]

Arduino des outputs

Quand les seuils sont atteints, le Arduino des inputs envoie des commandes sous forme de string au Arduino des output, qui exécute les commandes.

L’ajout d’engrais

Les engrais s’ajoutent un après l’autre lorsque le seuil maximum de niveau d’eau est atteint. Le premier engrais s’ajoute selon le temps de déversement correspondant (voir section suivante). Lorsque le temps est écoulé, la variable fertilizer1Added passe à true, la valeur fertilizer1Available passe à false, et la valeur fertilizer2Available passe à true.

33

Le temps de déversement des engrais

Arduino des outputs

Il y a 3 fonctions addFertilizer() dans le code du Arduino des outputs, une pour chaque burette. Dans les fonctions correspondant aux engrais, la variable interval correspond au nombre de millisecondes (1/1000 de secondes) pendant lesquelles chaque engrais va se déverser. Entrez le nombre de secondes voulues multipliées par 1000 et n’oubliez pas de reprogrammer le Arduino (voir section plus haut).

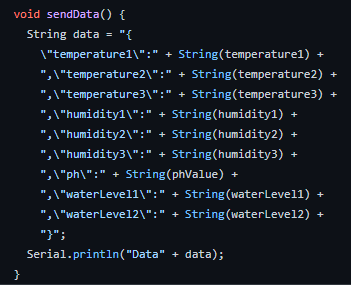
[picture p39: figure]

34

Il est important de ne pas toucher à l’intervalle dans la fonction addPhDown. L’intervalle de 500 millisecondes est vraiment le maximum pour ne pas que le phDown s’ajoute trop rapidement. Il ne sert à rien de choisir un intervalle plus petit parce que l’intervalle entre les itérations du Arduino est de 500 millisecondes.

L’envoie de données au Raspberry Pi

Les variables sont toutes envoyées au Raspberry Pi en même temps selon l’intervalle défini dans la fonction sendData de l’Arduino des inputs. Les variables sont envoyées dans le print du moniteur sériel.

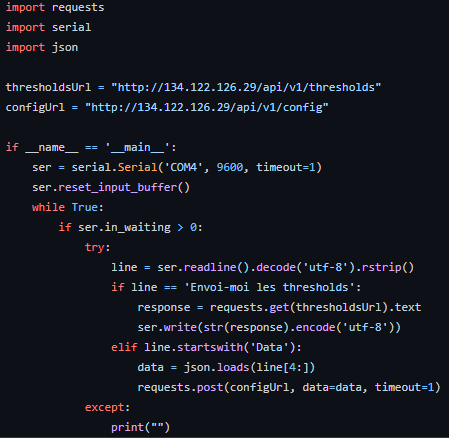
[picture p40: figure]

35

La réception des données

Le Raspberry Pi écoute sur le moniteur sériel du Arduino des Inputs. Lorsque l’Arduino envoi les données, le Raspberry Pi les lit pour ensuite les envoyer au serveur dans la collection config.

36

## Communication externe (Raspberry Pi)

## Le physique

Le « Raspberry Pi » est responsable de la communication entre le serveur sur le nuage et la serre

Hydra. Il accomplit cela en communiquant avec un Arduino et avec le nuage à l’aide d’une connexion

Wifi. Ainsi, le « Raspberry Pi » n’est qu’une passerelle entre plusieurs technologies qui fonctionne

différemment, un peu comme un traducteur.

La connexion au Arduino
L’Arduino des Inputs doit être brancher dans le port USB du Raspberry Pi. Il faut brancher l’Arduino

avant d’allumer le Raspberry Pi pour que le script marche.

La connexion Wifi
La connexion au Wifi devrait se faire automatiquement après un certain temps. Si c’est la première fois qu’il est allumé ou connecter au réseau en question, il faudra le connecter, en utilisant un écran, un clavier et une souris.

L’alimentation
Pour fonctionner correctement, le Raspberry Pi a besoin d’être branché à l’électricité. Sa source de courant se situe sous la trappe avec le reste des composants électriques. Il peut être fermé ou rallumé à l’aide de l’interrupteur vert dans le panneau de contrôle.

Perte de connexion (dépannage)
Dans ce cas, il est probable que votre Hydra se soit déconnectée de son serveur. Pour la reconnexion, vous devez fermer le Raspberry Pi (se contrôle avec l’interrupteur vert dans le panneau de contrôle) et les Arduinos (se contrôle avec l’interrupteur rouge toujours dans le panneau de contrôle). Par la suite, attendez environ cinq secondes. Pour terminer, vous pouvez réactiver les Arduinos (bleu) suivis du Raspberry Pi (Vert). Votre Hydra devrait recommencer à communiquer.

37

## Schéma de communications

Explication générale

Si un problème semble émerger de la communication entre 2 composants, il est possible que des ajustements doivent être faits à un niveau particulier. Pour ce faire, ce guide va tenter de vous expliquer la communication complète entre tous les différents composants. Pour une vue d’ensemble des communications vous pouvez vous referez à la figure #4.

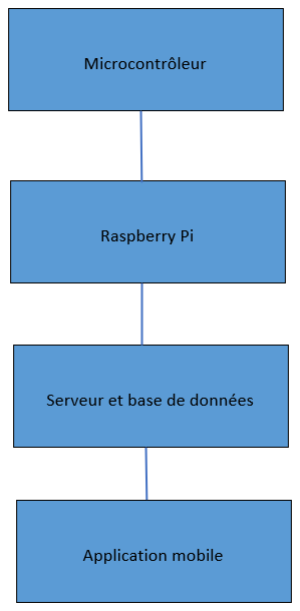
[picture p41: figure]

Figure #4 : Schéma des communications

#1 Arduino

En premier lieu, le Arduino connecté au Raspberry Pi peut recevoir des données également en envoyé. Si les informations des capteurs ne semblent pas être valides, la première étape est de vérifier l’intégrité de ces derniers sur le Arduino.

38

#2 Raspberry Pi

Par la suite, ces informations sont passées au Raspberry Pi. Très peu de processus et de calcul se passe à ce niveau, à moins d’une déconnexion complète, le problème n’est probablement pas de ce côté. (Pour résoudre une déconnexion complète veuillez-vous référez à la section : Perte de connexion (dépannage))

#3 Serveur

Cependant, il est tout de même possible qu’un problème émerge au niveau du serveur HTTP. Par exemple, si la modification de la serre à partir de l’application mobile ne s’exécute pas ou si les données sont reçues, mais pas actualisé. Dans ce cas il est nécessaire de s’assurer que la base de données est encore fonctionnelle et que l’objet JSON est encore adéquat (voir section : Base de données).

#4 Application mobile

Et finalement, l’application mobile. Cette dernière pourrait être la source de certains problèmes notamment par son côté réseau, il est possible que le réseau que vous utilisez peut bloquer la requête de cette dernière au serveur causant un dysfonctionnement de toutes les fonctions de l’application mobile.

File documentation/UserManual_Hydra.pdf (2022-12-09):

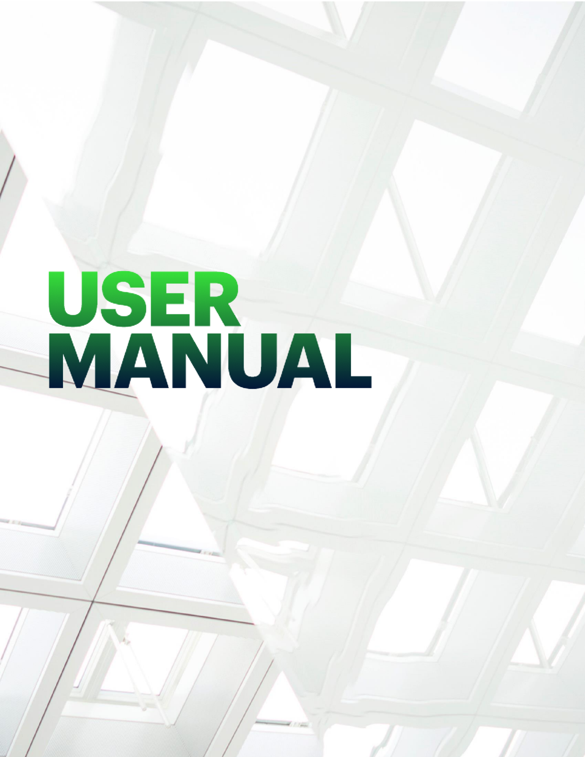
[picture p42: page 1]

2

## TABLE DES MATIÈRES

Utilisation de l’application mobile | 3
Visualiser les données | 3
Envoyer des données | 4
Utilisation de la serre physique | 5
Placer les plantes | 5
Entretien minimum | 5
Entreposage et hivernisation | 7
Retirer le filtreur | 7
Mettre l’antigel | 7
Pour une Hydra en santé | 8

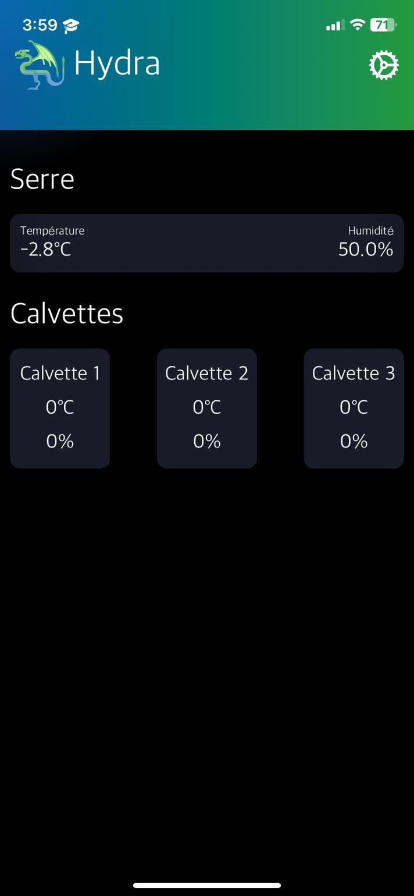
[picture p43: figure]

3

## Utilisation de l’application mobile

## Visualiser les données

Ici, vous pouvez visualiser les informations disponibles pour votre serre.

La température sous la section serre correspond aux
données d’OpenWeatherMaps Api pour la ville de Saint-Ours.

Pour chaque calvette, vous pouvez voir la température et l’humidité captées par le Dht11 dans la calvette.

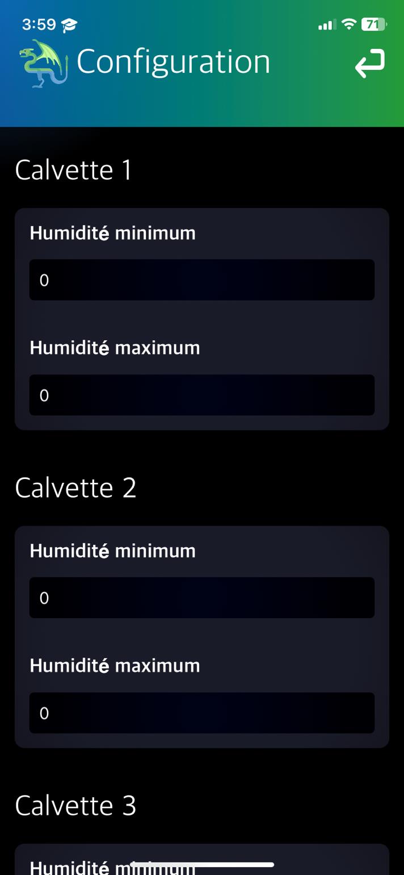
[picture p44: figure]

4

## Envoyer des données

Ici vous pouvez configurer les valeurs d’humidité et de ph de la serre.

Pour chaque calvette, l’humidité minimum correspond à la valeur d’humidité à partir de laquelle les buses vont commencer à arroser les plantes. L’humidité maximum correspond à la valeur à partir de laquelle les buses s’arrêtent.

Pour envoyer vos changements, faites défiler l’écran jusqu’au bas complètement et appuyez sur le bouton sauvegarder pour envoyer vos changements au serveur.

5

## Utilisation de la serre physique

## Placer les plantes

Des pots en plastiques contenant des billes d’argile sont mis à la disposions des utilisateurs de la serre Hydra. Pour planter, veuillez en premier lieu noter quelle clavette vous souhaitez utiliser pour pouvoir configurer les paramètres pour votre type de plantes. Veuillez également ne pas retirer des plantes d’autre utilisateur de la serre.

Avant de placer vos plantes dans les billes d’argiles, il est important de s’assurer que ces dernières possèdent des racines suffisamment longues pour pouvoir accéder au flux d’engrais des buses.

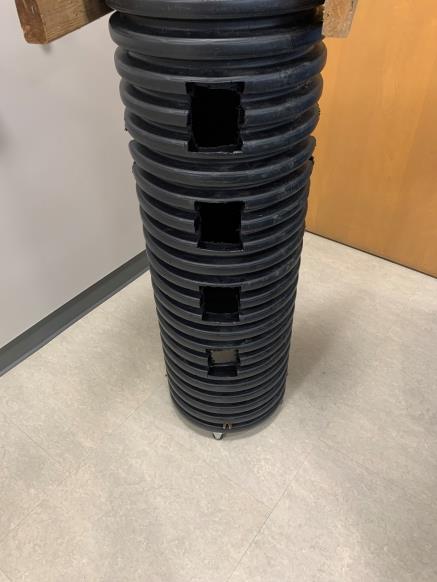
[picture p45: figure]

## Entretien minimum

Il est important qu’au moins une fois par jour, les clavettes soient tournées d’environ 180 degrés. Dans l’optique de permettre à toutes les plantes d’être à un moment de la journée directement sous la lumière du soleil

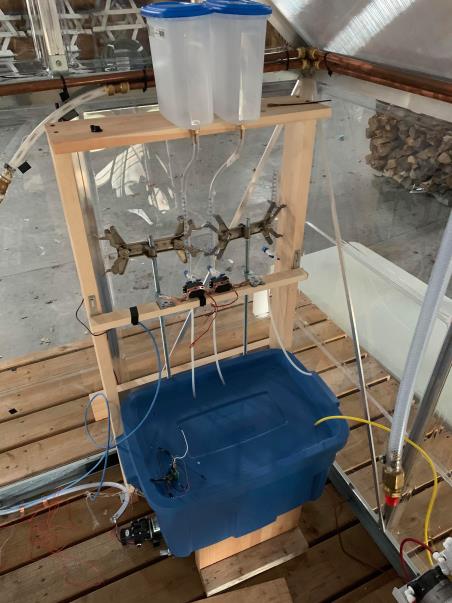
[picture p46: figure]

Remplir les bacs reliés aux burettes. À partir de la gauche, ajouter Flora Bloom dans la 1re burette, Flora Gro dans la 2e burette, Flora Micro dans la 3e burette et pH Down dans la 4e burette.

6

Bac avec 3 burettes et 2 réservoirs installés
Vérifier si les capteurs sont en place et fonctionnels (lumière allumée). Il y a un capteur de température et d’humidité fixé à chaque buse, deux capteurs de niveau d’eau dans le bac et un capteur de ph dans le bac

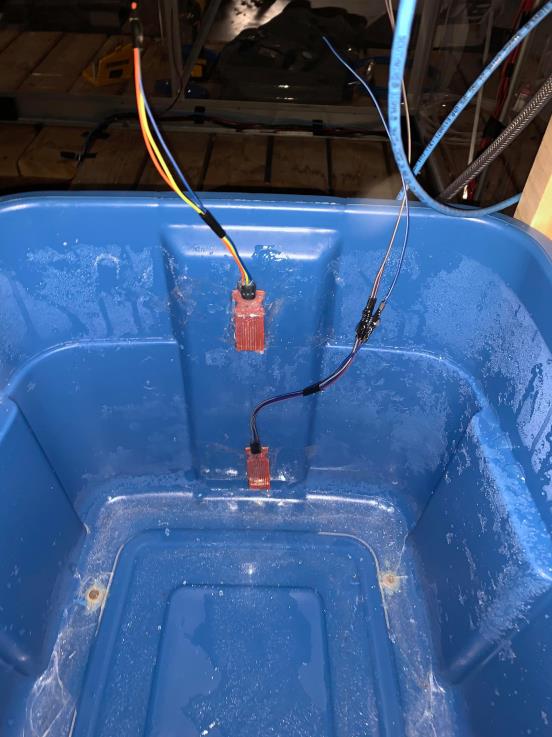
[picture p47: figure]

Capteurs de niveau d’eau

7

## Entreposage et hivernisation

## Retirer le filtreur

Avant de retirer le filtreur de sa plateforme de bois, il faut vider l’eau des tuyaux en pompant le reste d’eau dans les tuyaux du filtreur (seulement faire la pompe sans avoir d’entrée d’eau durant quelques secondes). Il faut vider l’eau des trois réservoirs en les dévissant, vous devez les remettre en place par la suite. Après, il faut vider et débrancher ses 2 fils d’alimentation et par la suite, placer le filtreur dans un endroit chauffé pour l’hiver.

## Mettre l’antigel

Si l’Hydra passe l’hiver dans un environnement proche ou

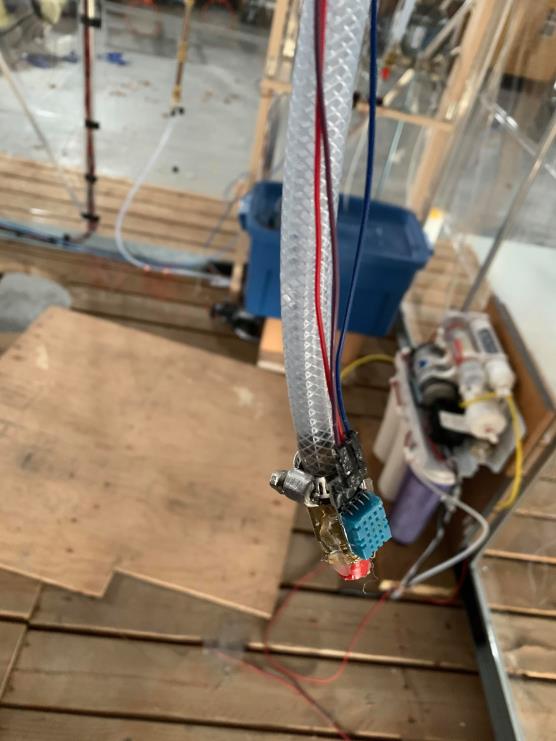
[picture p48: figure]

sous zéro degré Celsius, il sera important de mettre de l’antigel dans sa tuyauterie. Il est très important d’utiliser de l’antigel à base de PROPYLÈNE GLYCOL et non à base d’ÉTHYLÈNE GLYCOL. Le glycol à base d’éthylène est toxique et peut causer des dommages sévères aux plantes. Nous recommandons l’antigel (Glycol North American) comme il est non dommageable. Il est même utilisé dans des aliments non périssables.

h t t p s : / / w w w . i n g r e d i e n t d e p o t . c o m / p r o d u c t s / g l y c o l - 9 9 - 9 - 2 0 - l i t r e s (https://www.ingredientdepot.com/products/glycol-99-9-20-litres?variant=31848798650440&currency=CAD) ? variant=31848798650440&currency=CAD&utm_medium=product_sync&utm_source=google&utm_content=sag_organic &utm_campaign=sag_organic&utm_campaign=gs-2020-05-30&utm_source=google&utm_medium=smart_campaign (https://www.ingredientdepot.com/products/glycol-99-9-20-litres?variant=31848798650440&currency=CAD)

Une fois que vous avez choisi votre antigel, vous devrez en verser dans le bac
contenant l’eau des plantes préalablement vidé. Par la suite vous allez devoir
forcer le démarrage de la pompe qui alimente les plantes en eau pour remplacer l’eau déjà présente dans le système par l’antigel. Un bouton de couleur rouge, se trouvant dans le panneau de contrôle, vous permettra d’activer la pompe. Vous devez laisser la pompe fonctionner jusqu’à ce que

Vider le bac contenant l’eau des plantes

8

les buses remplacent leur jet d’eau par un jet d’antigel. Si le bac, contenant maintenant l’antigel, se vide trop tôt, arrêtez la pompe, ajouter de l’antigel dans le bac et redémarrez la pompe. Répétez ce procédé autant de fois si besoin.

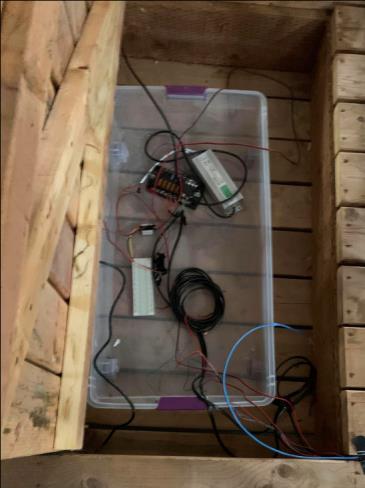
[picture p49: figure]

## Pour une Hydra en santé

Si vous voulez garder votre Hydra en bon état, nous recommandons l’utilisation de silice lors de la période de dégel pour absorber l’humidité et empêcher l’apparition de rouille sur l’électronique. Pour éviter l’apparition de cette rouille, nous recommandons de placer de la silice réutilisable dans le bac hermétique sous la trappe contenant la majorité de l’électronique. Si la fonte des neiges n’est toujours pas finie et que la silice a absorbé son maximum d’humidité, placez en un deuxième et faites sécher le premier. Quand le sera temps de ressortir votre Hydra, il ne sera plus nécessaire de garder la silice celle-ci, vous pouvez donc la ragé jusqu’à l’année prochaine.

## Dépannage

Mon Hydra ne se connecte plus au réseau et/ou les informations sur la serre dans l’application mobile ne sont plus à jour.

Dans ce cas, il est probable que votre Hydra se soit déconnectée de son serveur. Pour la reconnexion, vous devez fermer le Raspberry Pi (se contrôle avec l’interrupteur vert dans le panneau de contrôle) et les Arduinos (se contrôle avec l’interrupteur rouge toujours dans le panneau de contrôle). Par la suite, attendez environ cinq secondes. Pour terminer, vous pouvez réactiver les Arduinos (bleu) suivis du Raspberry Pi (Vert). Pour s’assurer le plus possible de la réussite de cette opération, il est possible d’attendre une ou deux secondes entre le redémarrage du Arduino et du Raspberry Pi. Votre Hydra devrait recommencer à communiquer.

Mes plantes sont déshydratées, ne sont pas suffisamment arrosées.

Peut-être que vous avez configuré les seuils d’humidité trop bas avec votre application mobile. Vérifiez aussi que votre seuil de pH correspond à une valeur réaliste.

Il est également possible que vous ayez placé vos plantes trop tôt dans leur cycle de maturité et qu’elle n’ait donc pas de racine suffisamment longue pour obtenir les nutriments fournis par la brume des buses.

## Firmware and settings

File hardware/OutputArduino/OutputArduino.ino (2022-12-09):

#include <SoftwareSerial.h>
#include <Servo.h>
#define FILTER_PUMP_RELAY_PIN 4
#define SPRAYER_PUMP_RELAY_PIN 5
#define SPRAYER1_SWITCH_PIN 6
#define SPRAYER2_SWITCH_PIN 7
#define SPRAYER3_SWITCH_PIN 8
#define SERVO1_PIN A0
#define SERVO2_PIN A1
#define SERVO3_PIN A2
#define SERVO4_PIN A3

Servo servo1;
Servo servo2;
Servo servo3;
Servo servo4;

SoftwareSerial mySerial(2, 3);

boolean fertilizer1Available = true;
boolean fertilizer1Added = false;
boolean fertilizer2Available = false;
boolean fertilizer2Added = false;
boolean fertilizer3Available = false;
boolean fertilizer3Added = false;
long fertilizerTimerStart = 0;
long phDownTimerStart = 0;
String input;

void setup() {
  Serial.begin(9600);
  mySerial.begin(9600);

  pinMode(FILTER_PUMP_RELAY_PIN, OUTPUT);
  pinMode(SPRAYER_PUMP_RELAY_PIN, OUTPUT);
  pinMode(SPRAYER1_SWITCH_PIN, OUTPUT);
  pinMode(SPRAYER2_SWITCH_PIN, OUTPUT);
  pinMode(SPRAYER3_SWITCH_PIN, OUTPUT);
  pinMode(SERVO1_PIN, OUTPUT);
  pinMode(SERVO2_PIN, OUTPUT);
  pinMode(SERVO3_PIN, OUTPUT);
  pinMode(SERVO4_PIN, OUTPUT);

  servo1.attach(SERVO1_PIN);
  servo1.write(90);
  servo2.attach(SERVO2_PIN);
  servo2.write(90);
  servo3.attach(SERVO3_PIN);
  servo3.write(90);
  servo4.attach(SERVO4_PIN);
  servo4.write(90);
}

void loop() {
  while (mySerial.available() > 0) {
    input = mySerial.readStringUntil('\n');
    input.trim();
    Serial.println("Input: " + input);

    if (input.equals("Filter pump on") ) {
      digitalWrite(FILTER_PUMP_RELAY_PIN, LOW);
      fertilizer1Available = true;
    }

    if (input.equals("Filter pump off")) {
      digitalWrite(FILTER_PUMP_RELAY_PIN, HIGH);
      if (fertilizer1Available) {
        addFertilizer1();
      }
      if (fertilizer2Available) {
        addFertilizer2();
      }
      if (fertilizer3Available) {
        addFertilizer3();
      }
    }

    if (input.equals("Sprayer1 on")) {
      digitalWrite(SPRAYER_PUMP_RELAY_PIN, LOW);
      digitalWrite(SPRAYER1_SWITCH_PIN, LOW);
    }

    if (input.equals("Sprayer1 off")) {
      digitalWrite(SPRAYER_PUMP_RELAY_PIN, HIGH);
      digitalWrite(SPRAYER1_SWITCH_PIN, HIGH);
    }

    if (input.equals("Sprayer2 on")) {
      digitalWrite(SPRAYER_PUMP_RELAY_PIN, LOW);
      digitalWrite(SPRAYER2_SWITCH_PIN, LOW);
    }

    if (input.equals("Sprayer2 off")) {
      digitalWrite(SPRAYER_PUMP_RELAY_PIN, HIGH);
      digitalWrite(SPRAYER2_SWITCH_PIN, HIGH);
    }

    if (input.equals("Sprayer3 on")) {
      digitalWrite(SPRAYER_PUMP_RELAY_PIN, LOW);
      digitalWrite(SPRAYER3_SWITCH_PIN, LOW);
    }

    if (input.equals("Sprayer3 off")) {
      digitalWrite(SPRAYER_PUMP_RELAY_PIN, HIGH);
      digitalWrite(SPRAYER3_SWITCH_PIN, HIGH);
    }

    if (input.equals("Add phDown") ) {
      addPhDown();
    }

    if (input.equals("Close phDown") ) {
      servo4.write(90);
    }
  }
  delay(500);
}

void addFertilizer1() {
  int interval = 82000;
  if (millis() - fertilizerTimerStart >= interval ) {
    Serial.println( millis() - fertilizerTimerStart );
    fertilizerTimerStart = millis();
    if (fertilizer1Added) {
      servo1.write(90);
      fertilizer1Available = false;
      fertilizer1Added = false;
      fertilizer2Available = true;
    }
  } else {
    servo1.write(0);
    fertilizer1Added = true;
  }
}

void addFertilizer2() {
  int interval = 82000;
  if (millis() - fertilizerTimerStart >= interval ) {
    fertilizerTimerStart = millis();
    if (fertilizer2Added) {
      servo2.write(90);
      fertilizer2Available = false;
      fertilizer2Added = false;
      fertilizer3Available = true;
    }
  } else {
    servo2.write(0);
    fertilizer2Added = true;
  }
}

void addFertilizer3() {
  int interval = 82000;
  if (millis() - fertilizerTimerStart >= interval ) {
    fertilizerTimerStart = millis();
    if (fertilizer3Added) {
      servo3.write(90);
      fertilizer3Available = false;
      fertilizer3Added = false;
    }
  } else {
    servo3.write(0);
    fertilizer3Added = true;
  }
}

void addPhDown() {
  int interval = 500;
  if ( millis() - phDownTimerStart > interval ) {
    phDownTimerStart = millis();
    servo4.write(0);
  } else {
    servo4.write(90);
  }
}

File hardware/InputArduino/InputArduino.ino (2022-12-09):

#include <SoftwareSerial.h>
#include <Adafruit_Sensor.h>
#include <DHT.h>
#include <DHT_U.h>
#include <ArduinoJson.h>
#define DHT11_PIN 8
#define SECOND_DHT11_PIN 9
#define THIRD_DHT11_PIN 10
#define DHTTYPE DHT11
#define WATER_SENSOR_PIN A1
#define WATER_SENSOR_POWER_PIN 7
#define WATER_SENSOR2_PIN A2
#define WATER_SENSOR2_POWER_PIN 4
#define PH_SENSOR A0

DHT dht1(DHT11_PIN, DHTTYPE);
DHT dht2(SECOND_DHT11_PIN, DHTTYPE);
DHT dht3(THIRD_DHT11_PIN, DHTTYPE );

SoftwareSerial mySerial(2, 3);

long receiveTimerStart = 0;

// Données de l'API
float humidityLowerTreshold1 = 85;
float humidityUpperTreshold1 = 95;
float humidityLowerTreshold2 = 85;
float humidityUpperTreshold2 = 95;
float humidityLowerTreshold3 = 85;
float humidityUpperTreshold3 = 95;
float waterLevelLowerTreshold = 70;
float waterLevelUpperTreshold = 550;
float phTreshold = 6.5;

// Données des capteurs
float phCalibration = 21.20;
float phValue;
float temperature1;
float temperature2;
float temperature3;
float humidity1;
float humidity2;
float humidity3;
float waterLevel1;
float waterLevel2;

void setup() {
  Serial.begin(9600);
  dht1.begin();
  dht2.begin();
  dht3.begin();

  pinMode(WATER_SENSOR_POWER_PIN, OUTPUT);
  digitalWrite(WATER_SENSOR_POWER_PIN, LOW);
  pinMode(WATER_SENSOR2_POWER_PIN, OUTPUT);
  digitalWrite(WATER_SENSOR2_POWER_PIN, LOW);

  delay(150);
}

void loop() {
  getThresholds();

  temperature1 = dht1.readTemperature();
  temperature1 = isnan(temperature1) ? 999 : temperature1;
  temperature2 = dht2.readTemperature();
  temperature2 = isnan(temperature2) ? 999 : temperature2;
  temperature3 = dht3.readTemperature();
  temperature3 = isnan(temperature3) ? 999 : temperature3;
  humidity1 = dht1.readHumidity();
  humidity1 = isnan(humidity1) ? 999 : humidity1;
  humidity2 = dht2.readHumidity();
  humidity2 = isnan(humidity2) ? 999 : humidity2;
  humidity3 = dht3.readHumidity();
  humidity3 = isnan(humidity3) ? 999 : humidity3;
  waterLevel1 = readWaterLevel();
  waterLevel1 = isnan(waterLevel1) ? 999 : waterLevel1;
  waterLevel2 = readSecondWaterLevel();
  waterLevel2 = isnan(waterLevel2) ? 999 : waterLevel2;
  phValue = readPh();
  phValue = isnan(phValue) ? 999 : phValue;

  sendData();

  if (waterLevel1 > waterLevelUpperTreshold) {
    mySerial.println("Filter pump off");
  }
  if (waterLevel2 < waterLevelLowerTreshold) {
    mySerial.println("Filter pump on");
  }
  if (humidity1 < humidityLowerTreshold1) {
    mySerial.println("Sprayer1 on");
  }
  if (humidity1 > humidityUpperTreshold1) {
    mySerial.println("Sprayer1 off");
  }
  if (humidity2 < humidityLowerTreshold2) {
    mySerial.println("Sprayer2 on");
  }
  if (humidity2 > humidityUpperTreshold2) {
    mySerial.println("Sprayer2 off");
  }
  if (humidity3 < humidityLowerTreshold3) {
    mySerial.println("Sprayer3 on");
  }
  if (humidity3 > humidityUpperTreshold3) {
    mySerial.println("Sprayer3 off");
  }
  if (phValue > phTreshold) {
    mySerial.println("Add phDown");
  } else {
    mySerial.println("Close phDown");
  }

  delay(1000);
}

float readWaterLevel() {
  digitalWrite(WATER_SENSOR_POWER_PIN, HIGH);
  delay(10);
  float waterLevel = analogRead(WATER_SENSOR_PIN);
  digitalWrite(WATER_SENSOR_POWER_PIN, LOW);
  return waterLevel;
}

float readSecondWaterLevel() {
  digitalWrite(WATER_SENSOR2_POWER_PIN, HIGH);
  delay(10);
  float waterLevel = analogRead(WATER_SENSOR2_PIN);
  digitalWrite(WATER_SENSOR2_PIN, LOW);
  return waterLevel;
}

float readPh() {
  int buf[10];
  for (int i = 0; i < 10; i++) {
    buf[i] = analogRead(PH_SENSOR);
    //delay(30); // use for a bigger average
  }
  bSort(buf, 10);
  return calculateAveragePh(buf, 10);
}

float calculateAveragePh(int *buf, int l) {
  unsigned long int avgValue = 0;
  for (int i = 2; i < l - 2; i++)
    avgValue += buf[i];
  float pHVol = (float)avgValue * 5.0 / 1024 / 6;
  float phValue = -5.70 * pHVol + phCalibration;
  return phValue;
}

void bSort(int *buf, short l) {
  int temp;
  for (int i = 0; i < l - 1; i++) {
    for (int j = i + 1; j < l; j++) {
      if (buf[i] > buf[j]) {
        temp = buf[i];
        buf[i] = buf[j];
        buf[j] = temp;
      }
    }
  }
}

void getThresholds() {
  Serial.println("Envoi-moi les thresholds");
  while (Serial.available() > 0) {
    String response = Serial.readString();
    Serial.flush();
    StaticJsonBuffer<400> jsonBuffer;
    JsonObject& root = jsonBuffer.parseObject(response);
    humidityLowerTreshold1 = root["humidityMinThreshold1"];
    humidityUpperTreshold1 = root["humidityMaxThreshold1"];
    humidityLowerTreshold2 = root["humidityMinThreshold2"];
    humidityUpperTreshold2 = root["humidityMaxThreshold2"];
    humidityLowerTreshold3 = root["humidityMinThreshold3"];
    humidityUpperTreshold3 = root["humidityMaxThreshold3"];
  }
}

void sendData() {
  String data = "{
    \"temperature1\":" + String(temperature1) + 
    ",\"temperature2\":" + String(temperature2) + 
    ",\"temperature3\":" + String(temperature3) + 
    ",\"humidity1\":" + String(humidity1) + 
    ",\"humidity2\":" + String(humidity2) + 
    ",\"humidity3\":" + String(humidity3) + 
    ",\"ph\":" + String(phValue) + 
    ",\"waterLevel1\":" + String(waterLevel1) + 
    ",\"waterLevel2\":" + String(waterLevel2) + 
    "}";
  Serial.println("Data" + data);
}

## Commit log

2019-11-25 Get à partir de la BD
2019-11-25 Ajout du tableau des matériaux
2019-11-26 broker update + connecting current routing to new broker
2019-12-02 Threshold et config dans la même collection.
2019-12-17 Ajout des fichiers Docker et suppression du logo du VOVLAB
2020-11-11 Bump dot-prop from 4.2.0 to 4.2.1 in /backend
    Bumps [dot-prop](https://github.com/sindresorhus/dot-prop) from 4.2.0 to 4.2.1.
    - [Release notes](https://github.com/sindresorhus/dot-prop/releases)
    - [Commits](https://github.com/sindresorhus/dot-prop/compare/v4.2.0...v4.2.1)
2020-11-11 first backend lte socket push
2020-11-26 fixed return to decimal for socket connection
2020-12-16 Added mobile plus arduino
2022-10-28 criss de refactor
2022-10-28 Feat: automatized database inserts
2022-10-28 Feat: arduinos
2022-11-04 feat: add clickable button
2022-11-18 Feat: added raspberry pi script
2022-11-25 Refactor: renamed button
2022-12-14 Refactor: renamed folder
    [Assemblage1.SLDASM, Section 2 sup bille.STL, Section 3 sup bille.STL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]
